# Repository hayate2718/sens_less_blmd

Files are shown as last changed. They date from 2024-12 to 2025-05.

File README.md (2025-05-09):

# センサレスブラシレスモータドライバの基板
FETドライブ基板、MCU基板を基板対基板コネクタでつなげることでモータシステムを構成している。
この構成の利点としては、故障の可能性が高いFETドライブ基板を切り離すことで運用コストの低下、高さ方向に基板をつなげることで下方占有面積の削減を目的としている。
特に、ヒートシンクや電源コネクタ等を基板に搭載すると高さ方向にデッドスペースが多く発生するためその有効利用となる。

## FETドライブ基板サイズ
58.5 x 78.4

## 取付穴ピッチ
52.5 x 49 M3

## 対応ヒートシンク
ヒートシンクの取り付けを前提とした設計をしており優れた放熱効果を実現する。
* ALPHA DCC5923Lシリーズ

## MCU基板インターフェース
* CAN通信用コネクタは2種類基板上に搭載しており、用途に応じて柔軟に対応可能としている。特にRJ45コネクタではCAN以外に12V電源ラインを有しておりLANケーブルのみでの通信電源確保を可能としている。<br>
* 過去にMDを設計した際、組み込みで使うIFのみしか用意しなかった結果ファームウェアの開発が非常にめんどくさくなったため、ロボット組み込み時は使わないがデバッグ用のUARTを装備している。<br>
* UART用の5ピンコネクタには、USB-UART変換によくついている5V電源を入力するピンがあり、5V出力を有するUSB-UART変換であればこれ単体でMCUの起動が可能である。<br>
* MCU基板単体でのデバッグ作業が可能なように電源入力用のコネクタを用意している。さらにFETドライブ基板側にも電源出力があり、GNDラインの絶縁を犠牲にすることでMCU側への電源供給が可能<br>
* MCU基板は5V系IC、3.3V系ICの2系が存在し、5V生成にスイッチング電源を利用し、電源入力を高電圧としバスの電流負荷を軽減することを狙っている。<br>

### 通信ライン
CAN,UART<br>
### 電源
PowerSupply 12V

### RJ45 ピンアサイン
POEのピンアサインに似せている
|Pin num|Function|
|---|---|
|1||
|2||
|3|CANL|
|4|Power_Supply|
|5|Power_Supply|
|6|CANH|
|7|GND|
|8|GND|

## MCUぺりふぇらるあさいん
|Pin num|Pin name|peripheral|note|
|----|----|----|----|
|1|RA7|GPIO IN|CAN ID1|
|2|RB14|NONE||
|3|RB15|QEICMP1|Unsupported|
|4|MCLR|||
|5|VSS|||
|6|VDD|||
|7|RA12|NONE||
|8|RA11|NONE||
|9|RA0|AN0|ADC W_CURRENT|
|10|RA1|NONE||
|11|RB0|AN2|ADC U_CURRENT|
|12|RB1|NONE||
|13|RB2|PGC1||
|14|RB3|PGD1||
|15|AVDD|||
|16|AVSS|||
|17|RC0|QEA1|Unsupported|
|18|RC1|INDX1|Unsupported|
|19|RC2|HOME1|Unsupported|
|20|RC11|NONE||
|21|VSS|||
|22|VDD|||
|23|RA8|QEB1|Unsupported|
|24|RB4|C1TX|CAN_TX|
|25|RA4|C1RX|CAN_RX|
|26|VDD|||
|27|RC12|OSCI||
|28|RC15|OSCO||
|29|VSS|||
|30|RD8|GPIO IN|MD_FAULT|
|31|RB5|GPIO OUT|STAT_LED|
|32|RB6|U1RX|UART_RX|
|33|RC10|NONE||
|34|RB7|U1TX|UART_TX|
|35|RC13|GPIO OUT|FF1_LED(bord err "only input")|
|36|RB8|GPIO OUT|FF2_LED(bord err "only input")|
|37|RB9|NONE||
|38|RC6|PWM6H|MCPWM AHI|
|39|RC7|PWM6L|MCPWM ALO|
|40|RC8|PWM5H|MCPWM BHI|
|41|RC9|PWM5L|MCPWM BLO|
|42|VSS|||
|43|VDD|||
|44|RB10|PWM3H|MCPWM CHI|
|45|RB11|PWM3L|MCPWM CLO|
|46|RB12|GPIO IN|CAN ID4|
|47|RB13|GPIO IN|CAN ID3|
|48|RA10|GPIO IN|CAN ID2|

* VSS IS GND,VDD IS POWER SUPPLY(3.3V),"NONE" MUST BE "INTERNAL PULLUP" OR "GPIO OUT"

## ファームウェアについて
### マイコンについて
MCUにはPIC32MK0512MCJ048を採用しており、32BitPICのなかモータ制御向けとして販売されているものである。<br>
特徴として、専用の直行エンコーダインターフェース(QEI)、モータ制御用PWM(MCPWM)、CANFDが搭載されている。<br>
今回は利用していないがQEIはカウンタパルスのほかにカウンタパルス間の測定も可能となっており、高速域、低速域の領域でエンコーダを有効に利用できるペリフェラルである。<br>
さらに、前回のカウンタリード値と現在のカウンタリード値の差分を記憶するレジスタもあり速度計算も非常に用意に実装可能である。<br>
**QEI便利だね**<br>
モータ制御用PWMではPWMのカウンタマッチ割り込みがあり、これをADCの変換フラグに利用することが可能である。<br>
つまり、センターアラインPWMを利用すればPWM波形の一番安定した場所でADCのデータをペリフェラルのみで取得可能であるということだ。<br>
**これは本当に便利**<br>
トリガポイントはさらに柔軟に設定可能なので、割り込みハンドラを処理するときにはすでに変換データが容易されている状態を作り出すことすら可能である。<br>

### 制御について
6パルスIPDを実装し、磁器突極性を問わず初期位置推定を可能としている。<br>
IPDによって、初期位置を検出し任意の進角で動作を開始し、オープンループで十分なBEMFを取得できる速度域まで動作させる。（ここまではできた）<br>
そこから、FOCに遷移する。予定だった。ort

## コメント
いろいろ能書き書いたけどファーム未完成<br>
現代制御なんもわからん

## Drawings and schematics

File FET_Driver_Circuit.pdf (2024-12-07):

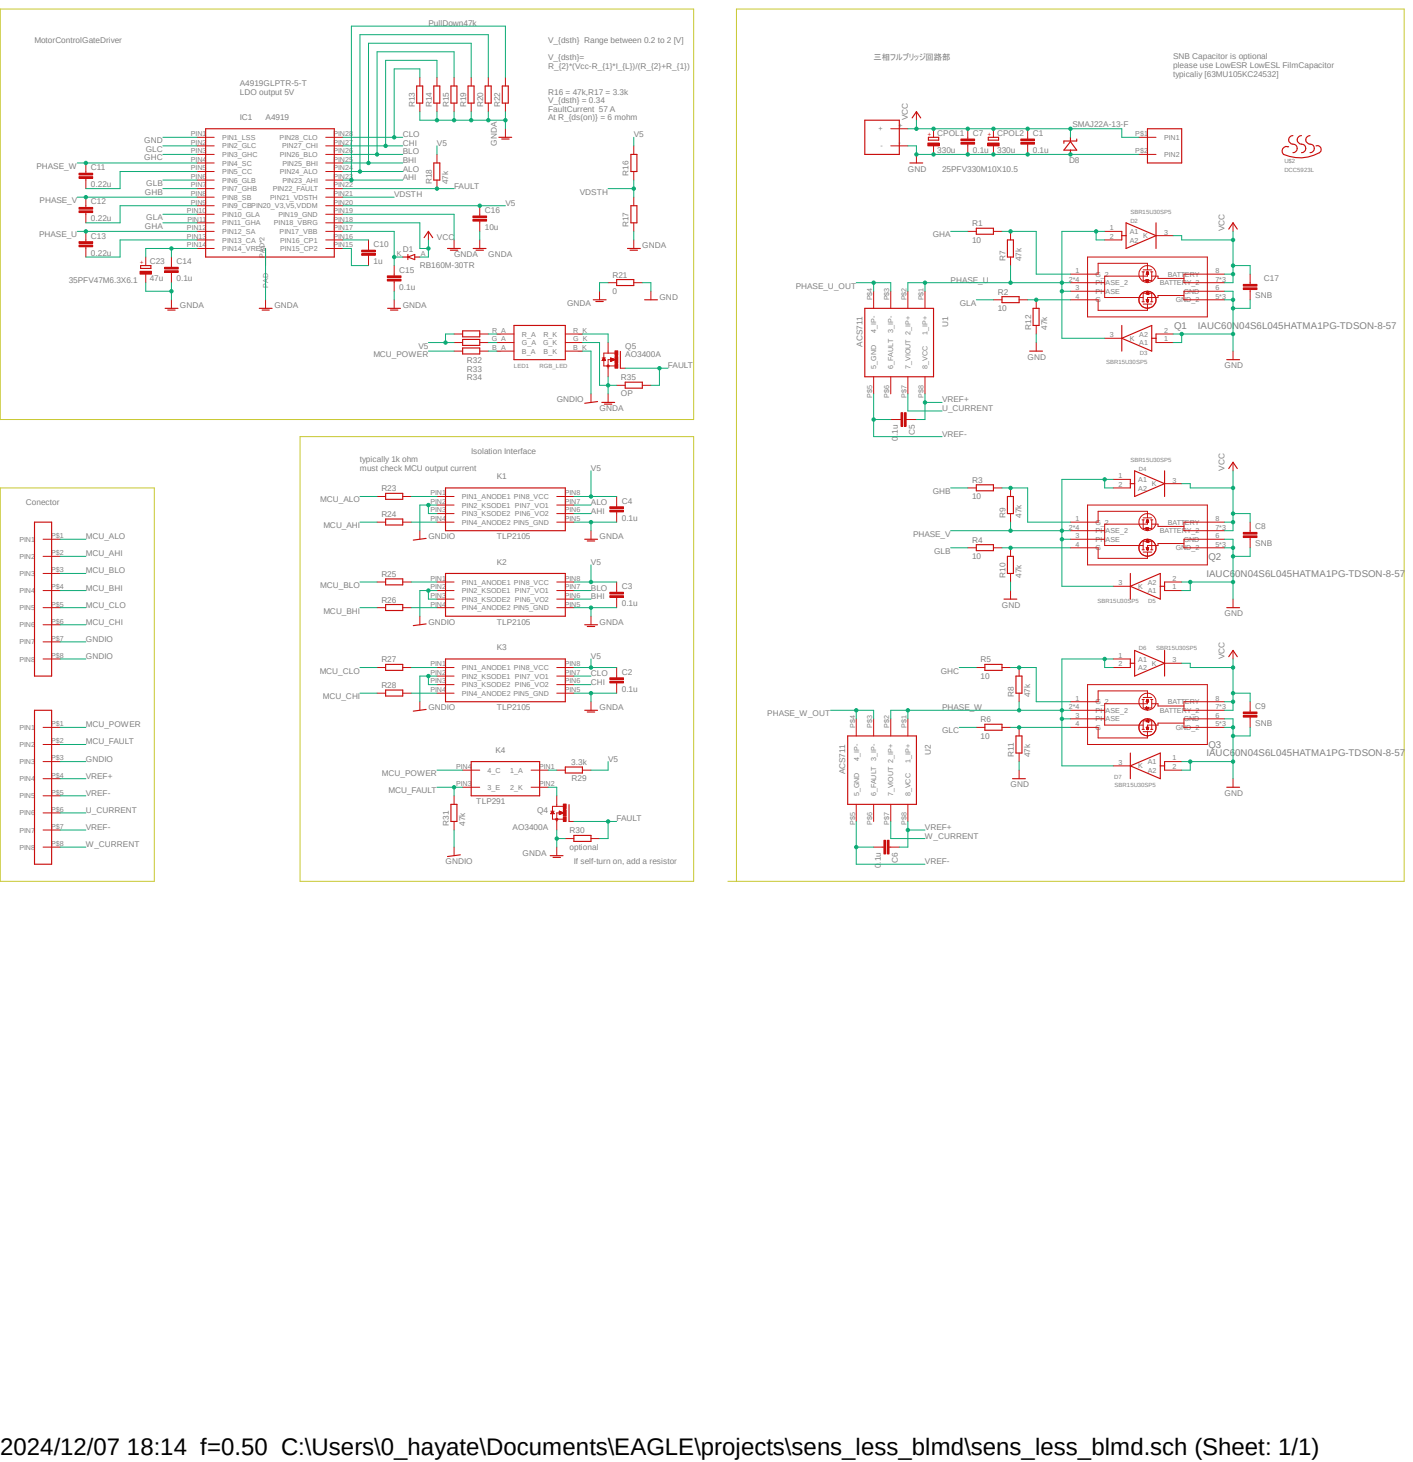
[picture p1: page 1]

SNB Capacitor is optional
please use LowESR LowESL FilmCapacitor
typicaliy [63MU105KC24532]

typically 1k ohm
must check MCU output current

If self-turn on, add a resistor

2024/12/07 18:14 f=0.50 C:\Users\0_hayate\Documents\EAGLE\projects\sens_less_blmd\sens_less_blmd.sch (Sheet: 1/1)

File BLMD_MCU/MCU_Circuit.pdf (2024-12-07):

MCU Debug Interface | UART Interface at 3.3V | MD Interface
Special Power Supply | Special CAN Interface

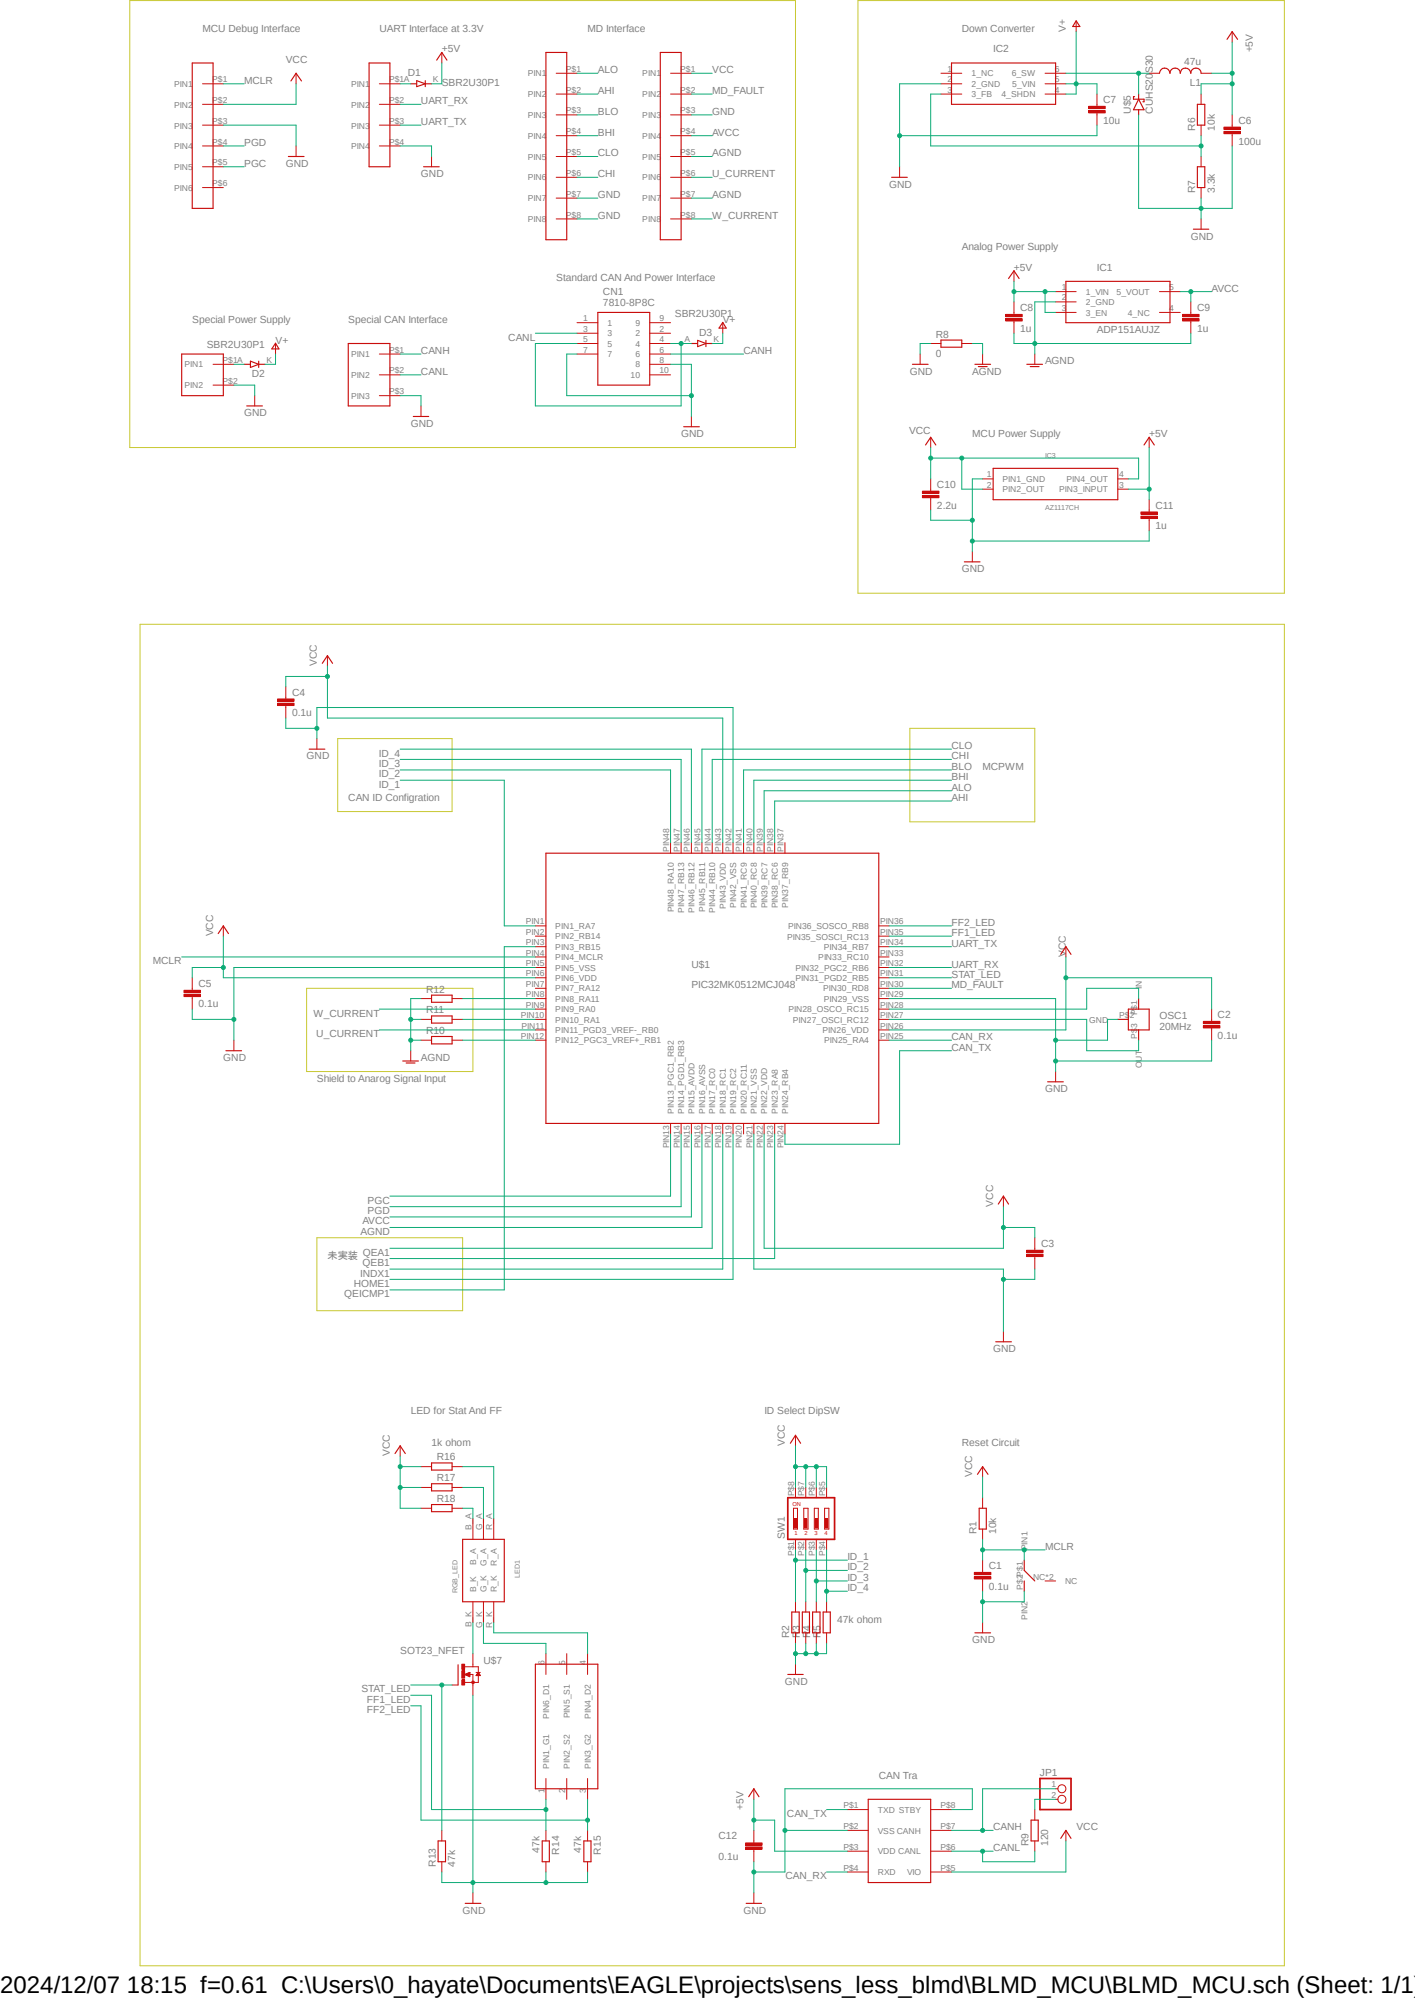
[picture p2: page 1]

Standard CAN And Power Interface

2_GND 2
3_EN 3

Shield to Anarog Signal Input

2024/12/07 18:15 f=0.61 C:\Users\0_hayate\Documents\EAGLE\projects\sens_less_blmd\BLMD_MCU\BLMD_MCU.sch (Sheet: 1/1)

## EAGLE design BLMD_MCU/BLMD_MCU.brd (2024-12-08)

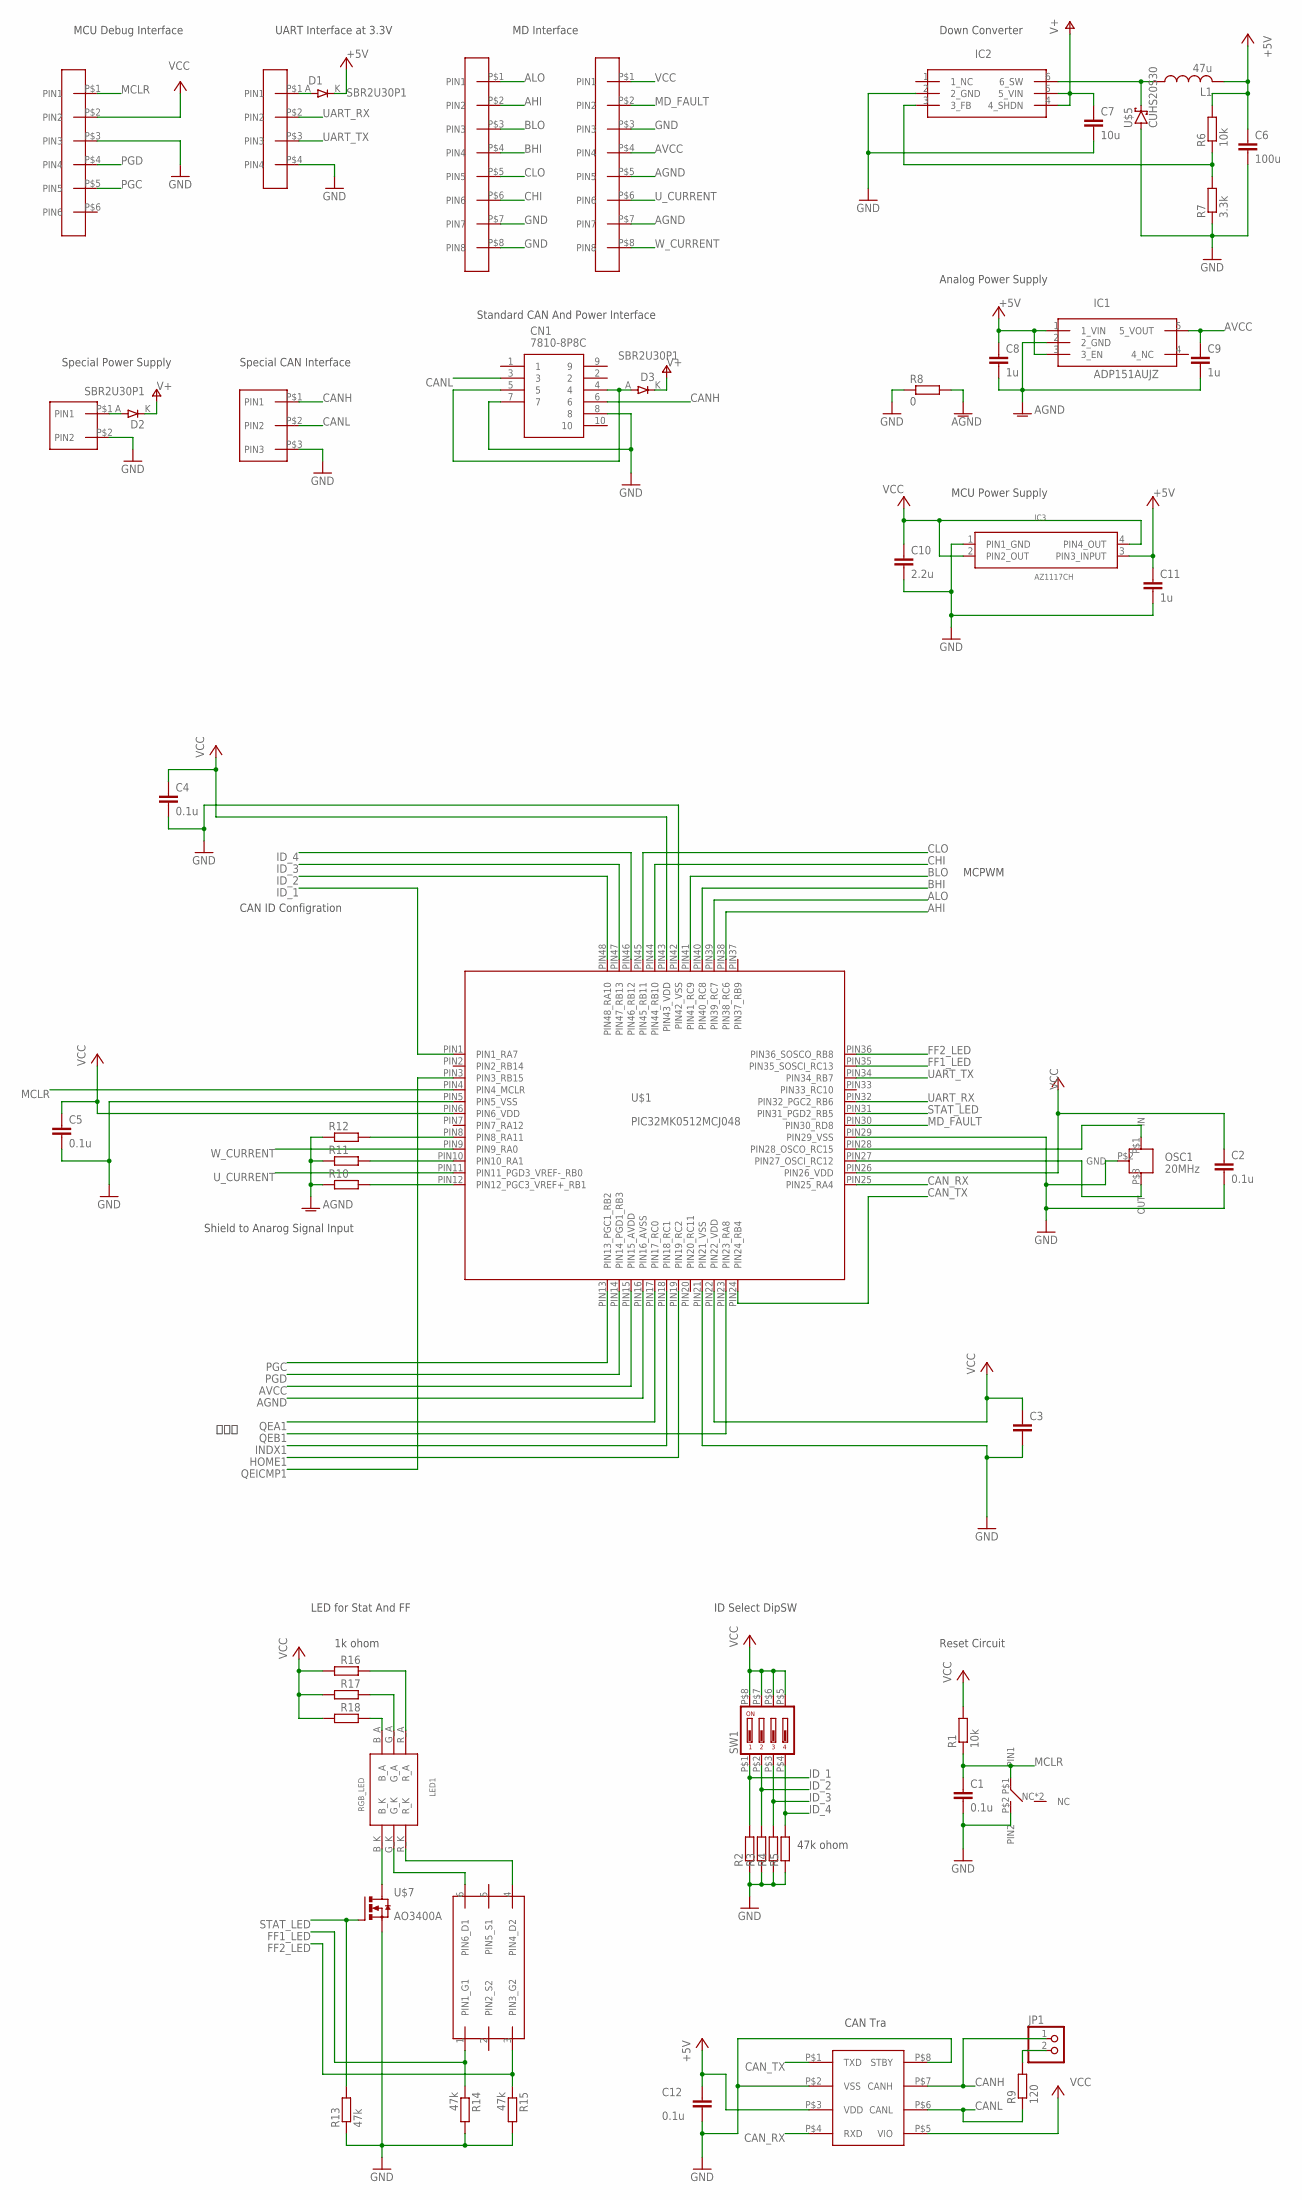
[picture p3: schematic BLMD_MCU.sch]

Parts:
C1, C2, C4, C5, C12: 0.1u; C1608
C3: C-EUC1608; C1608
C6: 100u; C3216
C7: 10u; C1608
C8, C9, C11: 1u; C1608
C10: 2.2u; C1608
CN1: 7810-8P8C; 78108P8C
CON1, CON2: JQ_S8P
CON3: XH_4P
CON4: XH_6P
CON5: XH_3P
D1, D2, D3: SBR2U30P1; SOD_123
IC1: ADP151AUJZ; SOT23-5
IC2: NJW1616T; SOT23-6
IC3: AZ1117CH; SOT223-W
IC4: MCP2562MCP2561-SN; SOIC8
JP1: PINHD-1X2; 1X02
L1: 47u; SMD_INDUCTOR
LED1: RGB_LED
OSC1: 20MHz; CSTNE#
R1, R6: 10k; 1608
R2, R3, R4, R5, R10, R11, R12, R16, R17, R18: R_REG; 1608
R7: 3.3k; 1608
R8: 0; 1608
R9: 120; 1608
R13, R14, R15: 47k; 1608
SW1: DIPSW4
U$1: PIC32MK0512MCJ048; LQFP48PIN
U$2: TAKUTOSUITTI2
U$4: XH_2P
U$5: CUHS20S30; SOD323-W
U$6: FDC6305; SSOT6
U$7: AO3400A; SOT23

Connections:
+5V: C6.1, C8.1, C11.1, C12.1, D1.K (C), IC1.1 (1_VIN), IC1.3 (3_EN), IC3.3 (PIN3_INPUT), IC4.P$3 (VDD), L1.P$2 (2), R6.2
AGND: C8.2, C9.2, CON2.P$5 (PIN5), CON2.P$7 (PIN7), IC1.2 (2_GND), R8.2, R10.1, R11.1, R12.1, U$1.PIN16 (PIN16_AVSS)
AHI: CON1.P$2 (PIN2), U$1.PIN38 (PIN38_RC6)
ALO: CON1.P$1 (PIN1), U$1.PIN39 (PIN39_RC7)
AVCC: C9.1, CON2.P$4 (PIN4), IC1.5 (5_VOUT), U$1.PIN15 (PIN15_AVDD)
BHI: CON1.P$4 (PIN4), U$1.PIN40 (PIN40_RC8)
BLO: CON1.P$3 (PIN3), U$1.PIN41 (PIN41_RC9)
CANH: CN1.6, CON5.P$1 (PIN1), IC4.P$7 (CANH), JP1.1
CANL: CN1.3, CON5.P$2 (PIN2), IC4.P$6 (CANL), R9.1
CAN_RX: IC4.P$4 (RXD), U$1.PIN25 (PIN25_RA4)
CAN_TX: IC4.P$1 (TXD), U$1.PIN24 (PIN24_RB4)
CHI: CON1.P$6 (PIN6), U$1.PIN44 (PIN44_RB10)
CLO: CON1.P$5 (PIN5), U$1.PIN45 (PIN45_RB11)
FF1_LED: R14.1, U$1.PIN35 (PIN35_SOSCI_RC13), U$6.1 (PIN1_G1)
FF2_LED: R15.1, U$1.PIN36 (PIN36_SOSCO_RB8), U$6.3 (PIN3_G2)
GND: C1.2, C2.2, C3.2, C4.2, C5.2, C6.2, C7.2, C10.2, C11.2, C12.2, CN1.7, CN1.8, CON1.P$7 (PIN7), CON1.P$8 (PIN8), CON2.P$3 (PIN3), CON3.P$4 (PIN4), CON4.P$3 (PIN3), CON5.P$3 (PIN3), IC2.2 (2_GND), IC3.1 (PIN1_GND), IC4.P$2 (VSS), IC4.P$8 (STBY), OSC1.P$2 (GND), R2.1, R3.1, R4.1, R5.1, R7.1, R8.1, R13.1, R14.2, R15.2, U$1.PIN5 (PIN5_VSS), U$1.PIN21 (PIN21_VSS), U$1.PIN29 (PIN29_VSS), U$1.PIN42 (PIN42_VSS), U$2.P$2 (PIN2), U$4.P$2 (PIN2), U$5.A, U$7.PIN2 (PIN3_S)
HOME1: U$1.PIN19 (PIN19_RC2)
ID_1: R2.2, SW1.P$1 (1), U$1.PIN1 (PIN1_RA7)
ID_2: R3.2, SW1.P$2 (2), U$1.PIN48 (PIN48_RA10)
ID_3: R4.2, SW1.P$3 (3), U$1.PIN47 (PIN47_RB13)
ID_4: R5.2, SW1.P$4 (4), U$1.PIN46 (PIN46_RB12)
INDX1: U$1.PIN18 (PIN18_RC1)
MCLR: C1.1, CON4.P$1 (PIN1), R1.1, U$1.PIN4 (PIN4_MCLR), U$2.P$1 (PIN1)
MD_FAULT: CON2.P$2 (PIN2), U$1.PIN30 (PIN30_RD8)
unnamed: R12.2, U$1.PIN8 (PIN8_RA11)
unnamed: R11.2, U$1.PIN10 (PIN10_RA1)
unnamed: LED1.B_A, R18.2
unnamed: R10.2, U$1.PIN12 (PIN12_PGC3_VREF+_RB1)
unnamed: OSC1.P$3 (OUT), U$1.PIN27 (PIN27_OSCI_RC12)
unnamed: OSC1.P$1 (IN), U$1.PIN28 (PIN28_OSCO_RC15)
unnamed: LED1.G_A, R17.2
unnamed: JP1.2, R9.2
unnamed: IC2.6 (6_SW), L1.P$1 (1), U$5.C
unnamed: IC2.3 (3_FB), R6.1, R7.2
unnamed: LED1.R_A, R16.2
unnamed: LED1.B_K, U$7.PIN3 (PIN2_D)
unnamed: CON3.P$1 (PIN1), D1.A
unnamed: LED1.G_K, U$6.6 (PIN6_D1)
unnamed: LED1.R_K, U$6.4 (PIN4_D2)
unnamed: D2.A, U$4.P$1 (PIN1)
unnamed: CN1.4, CN1.5, D3.A
PGC: CON4.P$5 (PIN5), U$1.PIN13 (PIN13_PGC1_RB2)
PGD: CON4.P$4 (PIN4), U$1.PIN14 (PIN14_PGD1_RB3)
QEA1: U$1.PIN17 (PIN17_RC0)
QEB1: U$1.PIN23 (PIN23_RA8)
QEICMP1: U$1.PIN3 (PIN3_RB15)
STAT_LED: R13.2, U$1.PIN31 (PIN31_PGD2_RB5), U$7.PIN1 (PIN1_G)
UART_RX: CON3.P$2 (PIN2), U$1.PIN32 (PIN32_PGC2_RB6)
UART_TX: CON3.P$3 (PIN3), U$1.PIN34 (PIN34_RB7)
U_CURRENT: CON2.P$6 (PIN6), U$1.PIN11 (PIN11_PGD3_VREF-_RB0)
V+: C7.1, D2.K (C), D3.K (C), IC2.4 (4_SHDN), IC2.5 (5_VIN)
VCC: C2.1, C3.1, C4.1, C5.1, C10.1, CON2.P$1 (PIN1), CON4.P$2 (PIN2), IC3.2 (PIN2_OUT), IC3.4 (PIN4_OUT), IC4.P$5 (VIO), R1.2, R16.1, R17.1, R18.1, SW1.P$5 (5), SW1.P$6 (6), SW1.P$7 (7), SW1.P$8 (8), U$1.PIN6 (PIN6_VDD), U$1.PIN22 (PIN22_VDD), U$1.PIN26 (PIN26_VDD), U$1.PIN43 (PIN43_VDD)
W_CURRENT: CON2.P$8 (PIN8), U$1.PIN9 (PIN9_RA0)

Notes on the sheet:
Shield to Anarog Signal Input
未実装
47k ohom
1k ohom
MCPWM
CAN ID Configration
MD Interface
UART Interface at 3.3V
MCU Debug Interface
Special Power Supply
Special CAN Interface
Standard CAN And Power Interface
Analog Power Supply
MCU Power Supply
Down Converter
LED for Stat And FF
ID Select DipSW
Reset Circuit
CAN Tra

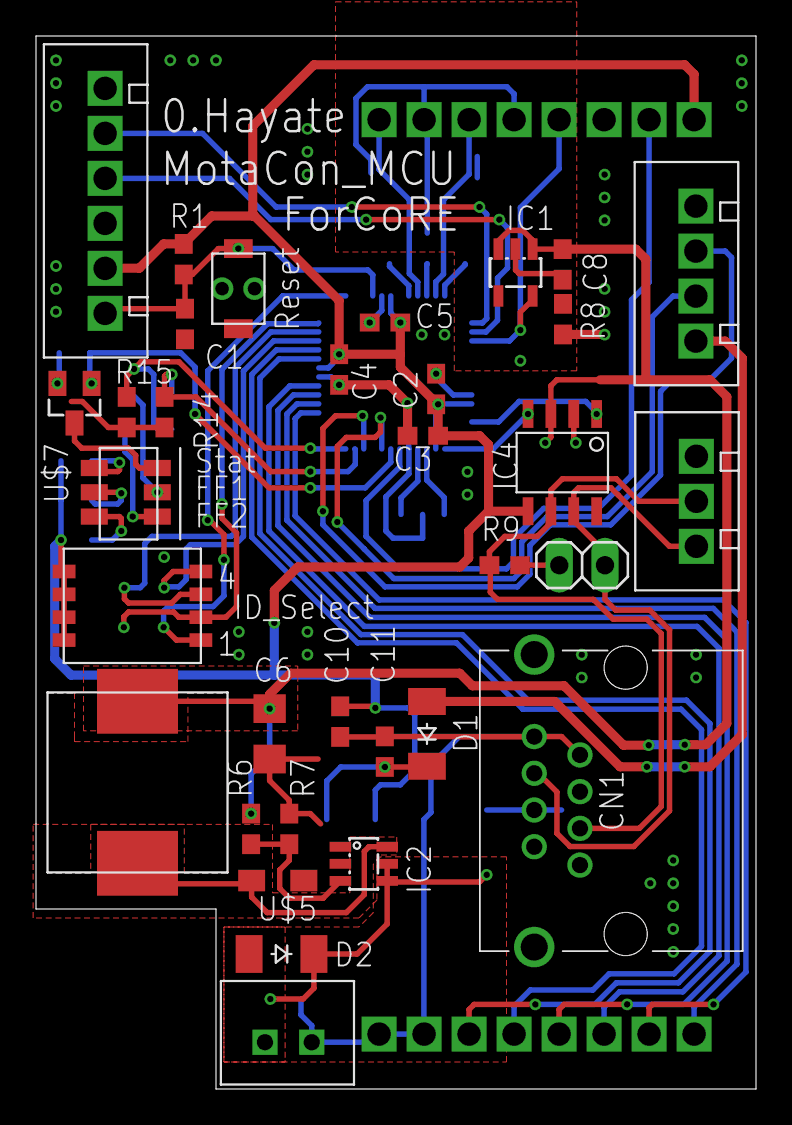
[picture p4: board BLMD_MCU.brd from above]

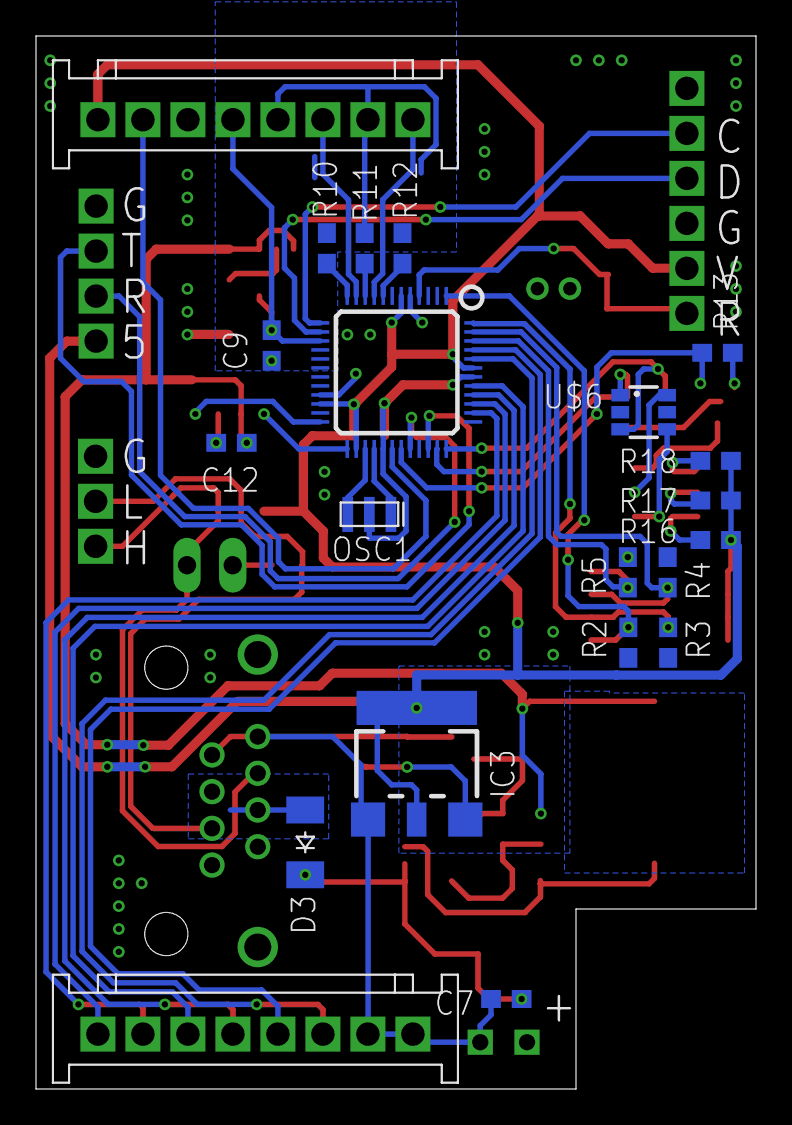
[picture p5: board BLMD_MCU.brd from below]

Board: 2 copper layers, 40.0 x 58.5 mm, 54 parts (21 on the bottom side), 48 nets.

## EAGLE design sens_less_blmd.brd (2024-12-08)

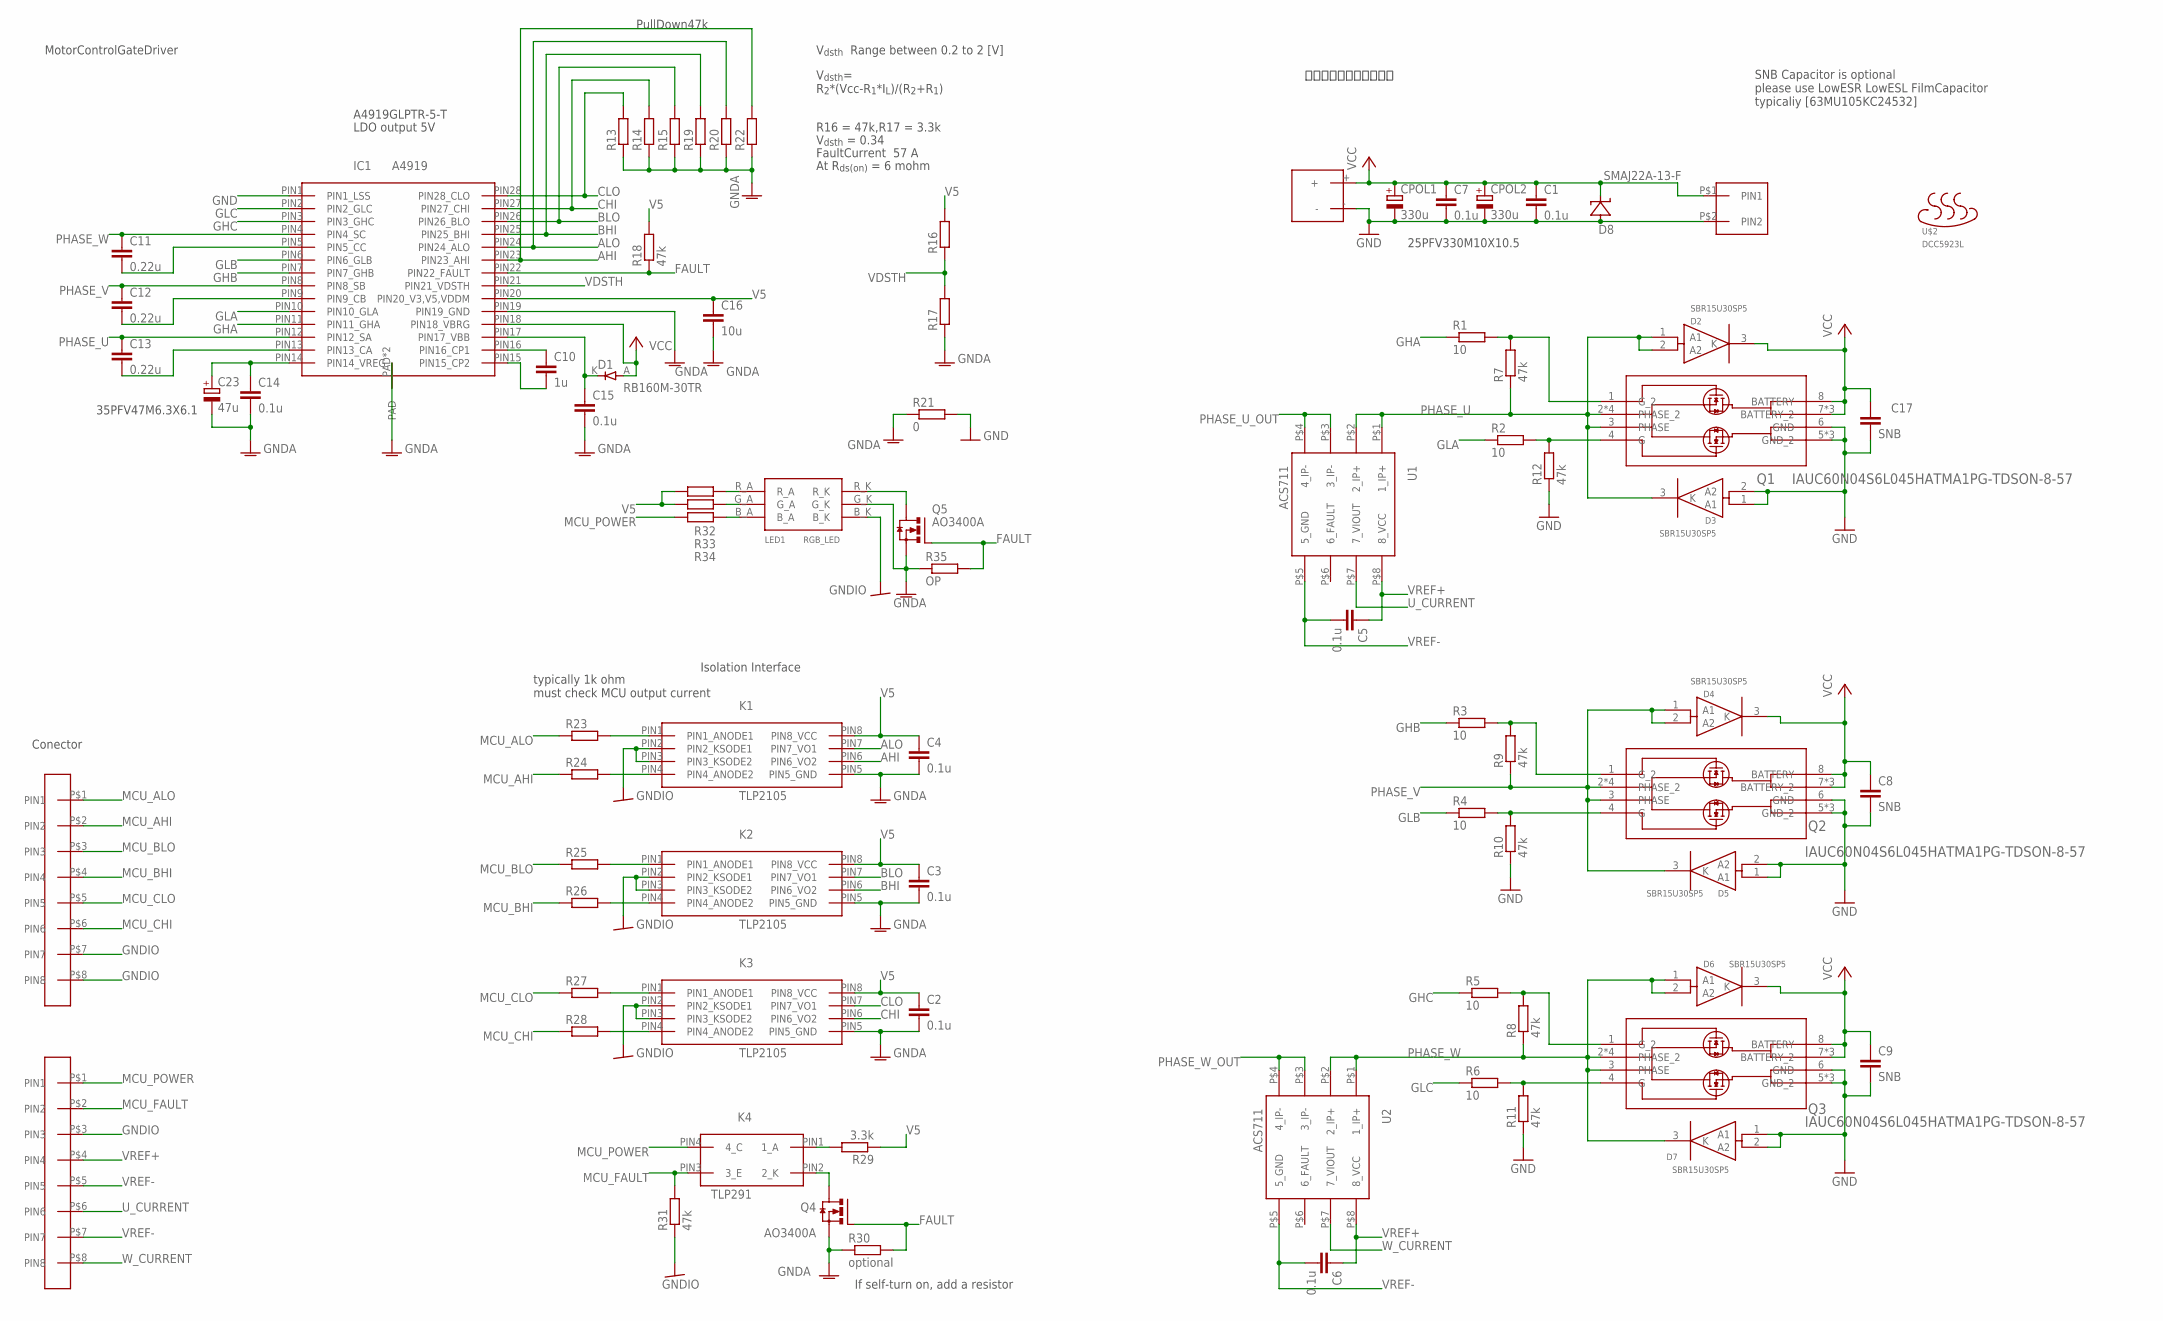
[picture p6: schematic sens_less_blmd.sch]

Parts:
C1, C2, C3, C4, C5, C6, C7, C14, C15: 0.1u; C1608
C8, C9, C17: SNB; C4532
C10: 1u; C1608
C11, C12, C13: 0.22u; C1608
C16: 10u; C1608
C23: 47u; 153CLV-0605
CON1, CON2: XH_8P
CPOL1, CPOL2: 330u; 1014CAPA
D1: RB160M-30TR; SOD_123
D2, D3, D4, D5, D6, D7: SBR15U30SP5; POWERDI_5
D8: SMAJ22A-13-F; DO-214AC
IC1: A4919; TSSOP_28P_ALLEGRO_E
K1, K2, K3: TLP2105; SOP8
K4: TLP291
LED1: RGB_LED
Q1, Q2, Q3: IAUC60N04S6L045HATMA1PG-TDSON-8-57; PG-TDSON-8-57
Q4, Q5: AO3400A; SOT23
R1, R2, R3, R4, R5, R6: 10; 1608
R7, R8, R9, R10, R11, R12, R18, R31: 47k; 1608
R13, R14, R15, R16, R17, R19, R20, R22, R23, R24, R25, R26, R27, R28, R32, R33, R34: R_REG; 1608
R21: 0; 1608
R29: 3.3k; 1608
R30: optional; 1608
R35: OP; 1608
U1, U2: ACS711; SOIC8
U$1: XH_2P
U$2: DCC5923L
U$22: XT60

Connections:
AHI: IC1.PIN23 (PIN23_AHI), K1.PIN6 (PIN6_VO2), R22.2
ALO: IC1.PIN24 (PIN24_ALO), K1.PIN7 (PIN7_VO1), R20.2
BHI: IC1.PIN25 (PIN25_BHI), K2.PIN6 (PIN6_VO2), R19.2
BLO: IC1.PIN26 (PIN26_BLO), K2.PIN7 (PIN7_VO1), R15.2
CHI: IC1.PIN27 (PIN27_CHI), K3.PIN6 (PIN6_VO2), R14.2
CLO: IC1.PIN28 (PIN28_CLO), K3.PIN7 (PIN7_VO1), R13.2
FAULT: IC1.PIN22 (PIN22_FAULT), Q4.PIN1 (PIN1_G), Q5.PIN1 (PIN1_G), R18.1, R30.2, R35.2
GHA: IC1.PIN11 (PIN11_GHA), R1.1
GHB: IC1.PIN7 (PIN7_GHB), R3.1
GHC: IC1.PIN3 (PIN3_GHC), R5.1
GLA: IC1.PIN10 (PIN10_GLA), R2.1
GLB: IC1.PIN6 (PIN6_GLB), R4.1
GLC: IC1.PIN2 (PIN2_GLC), R6.1
GND: C1.2, C7.2, C8.2, C9.2, C17.2, CPOL1.-, CPOL2.-, D3.1 (A1), D3.2 (A2), D5.1 (A1), D5.2 (A2), D7.1 (A1), D7.2 (A2), D8.A, IC1.PIN1 (PIN1_LSS), Q1.5 (GND_2), Q1.6 (GND), Q1.SPAD (GND_2), Q1.SPAD@1 (GND_2), Q2.5 (GND_2), Q2.6 (GND), Q2.SPAD (GND_2), Q2.SPAD@1 (GND_2), Q3.5 (GND_2), Q3.6 (GND), Q3.SPAD (GND_2), Q3.SPAD@1 (GND_2), R10.1, R11.1, R12.1, R21.2, U$1.P$2 (PIN2), U$22.-
GNDA: C2.2, C3.2, C4.2, C14.2, C15.2, C16.2, C23.-, IC1.PAD, IC1.PAD@14 (PAD), IC1.PIN19 (PIN19_GND), K1.PIN5 (PIN5_GND), K2.PIN5 (PIN5_GND), K3.PIN5 (PIN5_GND), LED1.G_K, Q4.PIN2 (PIN3_S), Q5.PIN2 (PIN3_S), R13.1, R14.1, R15.1, R17.1, R19.1, R20.1, R21.1, R22.1, R30.1, R35.1
GNDIO: CON1.P$3 (PIN3), CON2.P$7 (PIN7), CON2.P$8 (PIN8), K1.PIN2 (PIN2_KSODE1), K1.PIN3 (PIN3_KSODE2), K2.PIN2 (PIN2_KSODE1), K2.PIN3 (PIN3_KSODE2), K3.PIN2 (PIN2_KSODE1), K3.PIN3 (PIN3_KSODE2), LED1.B_K, R31.1
MCU_AHI: CON2.P$2 (PIN2), R24.1
MCU_ALO: CON2.P$1 (PIN1), R23.1
MCU_BHI: CON2.P$4 (PIN4), R26.1
MCU_BLO: CON2.P$3 (PIN3), R25.1
MCU_CHI: CON2.P$6 (PIN6), R28.1
MCU_CLO: CON2.P$5 (PIN5), R27.1
MCU_FAULT: CON1.P$2 (PIN2), K4.PIN3 (3_E), R31.2
MCU_POWER: CON1.P$1 (PIN1), K4.PIN4 (4_C), R34.1
unnamed: Q1.1 (G_2), R1.2, R7.2
unnamed: Q1.4 (G), R2.2, R12.2
unnamed: Q2.4 (G), R4.2, R10.2
unnamed: LED1.B_A, R34.2
unnamed: Q3.1 (G_2), R5.2, R8.2
unnamed: Q3.4 (G), R6.2, R11.2
unnamed: C10.1, IC1.PIN16 (PIN16_CP1)
unnamed: C10.2, IC1.PIN15 (PIN15_CP2)
unnamed: C14.1, C23.+, IC1.PIN14 (PIN14_VREG)
unnamed: K1.PIN1 (PIN1_ANODE1), R23.2
unnamed: K1.PIN4 (PIN4_ANODE2), R24.2
unnamed: K2.PIN1 (PIN1_ANODE1), R25.2
unnamed: K2.PIN4 (PIN4_ANODE2), R26.2
unnamed: K3.PIN1 (PIN1_ANODE1), R27.2
unnamed: C13.2, IC1.PIN13 (PIN13_CA)
unnamed: C12.2, IC1.PIN9 (PIN9_CB)
unnamed: C11.2, IC1.PIN5 (PIN5_CC)
unnamed: K3.PIN4 (PIN4_ANODE2), R28.2
unnamed: K4.PIN2 (2_K), Q4.PIN3 (PIN2_D)
unnamed: C15.1, D1.K (C), IC1.PIN17 (PIN17_VBB)
unnamed: K4.PIN1 (1_A), R29.2
unnamed: Q2.1 (G_2), R3.2, R9.2
unnamed: LED1.G_A, R33.2
unnamed: LED1.R_A, R32.2
unnamed: LED1.R_K, Q5.PIN3 (PIN2_D)
PHASE_U: C13.1, D2.1 (A1), D2.2 (A2), D3.3 (K), IC1.PIN12 (PIN12_SA), Q1.2 (PHASE_2), Q1.3 (PHASE), Q1.SDPAD (PHASE_2), Q1.SDPAD@1 (PHASE_2), Q1.SDPAD@2 (PHASE_2), R7.1, U1.P$1 (1_IP+), U1.P$2 (2_IP+)
PHASE_U_OUT: U1.P$3 (3_IP-), U1.P$4 (4_IP-)
PHASE_V: C12.1, D4.1 (A1), D4.2 (A2), D5.3 (K), IC1.PIN8 (PIN8_SB), Q2.2 (PHASE_2), Q2.3 (PHASE), Q2.SDPAD (PHASE_2), Q2.SDPAD@1 (PHASE_2), Q2.SDPAD@2 (PHASE_2), R9.1
PHASE_W: C11.1, D6.1 (A1), D6.2 (A2), D7.3 (K), IC1.PIN4 (PIN4_SC), Q3.2 (PHASE_2), Q3.3 (PHASE), Q3.SDPAD (PHASE_2), Q3.SDPAD@1 (PHASE_2), Q3.SDPAD@2 (PHASE_2), R8.1, U2.P$1 (1_IP+), U2.P$2 (2_IP+)
PHASE_W_OUT: U2.P$3 (3_IP-), U2.P$4 (4_IP-)
U_CURRENT: CON1.P$6 (PIN6), U1.P$7 (7_VIOUT)
V5: C2.1, C3.1, C4.1, C16.1, IC1.PIN20 (PIN20_V3,V5,VDDM), K1.PIN8 (PIN8_VCC), K2.PIN8 (PIN8_VCC), K3.PIN8 (PIN8_VCC), R16.2, R18.2, R29.1, R32.1, R33.1
VCC: C1.1, C7.1, C8.1, C9.1, C17.1, CPOL1.+, CPOL2.+, D1.A, D2.3 (K), D4.3 (K), D6.3 (K), D8.C, IC1.PIN18 (PIN18_VBRG), Q1.7 (BATTERY_2), Q1.8 (BATTERY), Q1.DPAD (BATTERY_2), Q1.DPAD@1 (BATTERY_2), Q2.7 (BATTERY_2), Q2.8 (BATTERY), Q2.DPAD (BATTERY_2), Q2.DPAD@1 (BATTERY_2), Q3.7 (BATTERY_2), Q3.8 (BATTERY), Q3.DPAD (BATTERY_2), Q3.DPAD@1 (BATTERY_2), U$1.P$1 (PIN1), U$22.+
VDSTH: IC1.PIN21 (PIN21_VDSTH), R16.1, R17.2
VREF+: C5.1, C6.1, CON1.P$4 (PIN4), U1.P$8 (8_VCC), U2.P$8 (8_VCC)
VREF-: C5.2, C6.2, CON1.P$5 (PIN5), CON1.P$7 (PIN7), U1.P$5 (5_GND), U2.P$5 (5_GND)
W_CURRENT: CON1.P$8 (PIN8), U2.P$7 (7_VIOUT)

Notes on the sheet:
三相フルブリッジ回路部
A4919GLPTR-5-T
LDO output 5V
PullDown47k
typically 1k ohm must check MCU output current
If self-turn on, add a resistor
Isolation Interface
MotorControlGateDriver
V_{dsth} Range between 0.2 to 2 [V]
At R_{ds(on)} = 6 mohm
V_{dsth}= R_{2}*(Vcc-R_{1}*I_{L})/(R_{2}+R_{1})
V_{dsth} = 0.34
FaultCurrent 57 A
R16 = 47k,R17 = 3.3k
Conector
SNB Capacitor is optional please use LowESR LowESL FilmCapacitor typicaliy [63MU105KC24532]
25PFV330M10X10.5
35PFV47M6.3X6.1

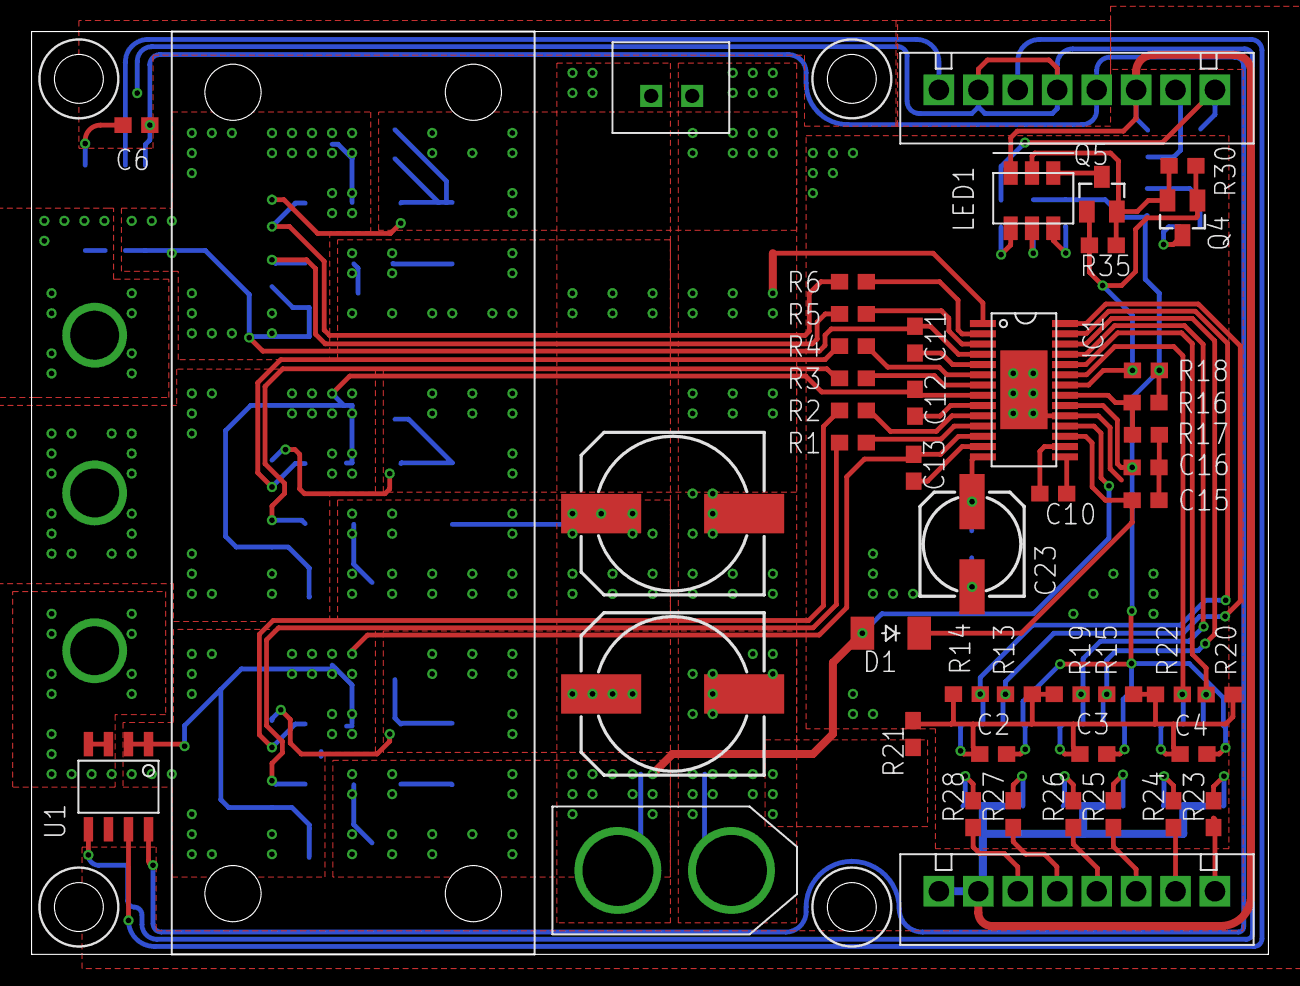
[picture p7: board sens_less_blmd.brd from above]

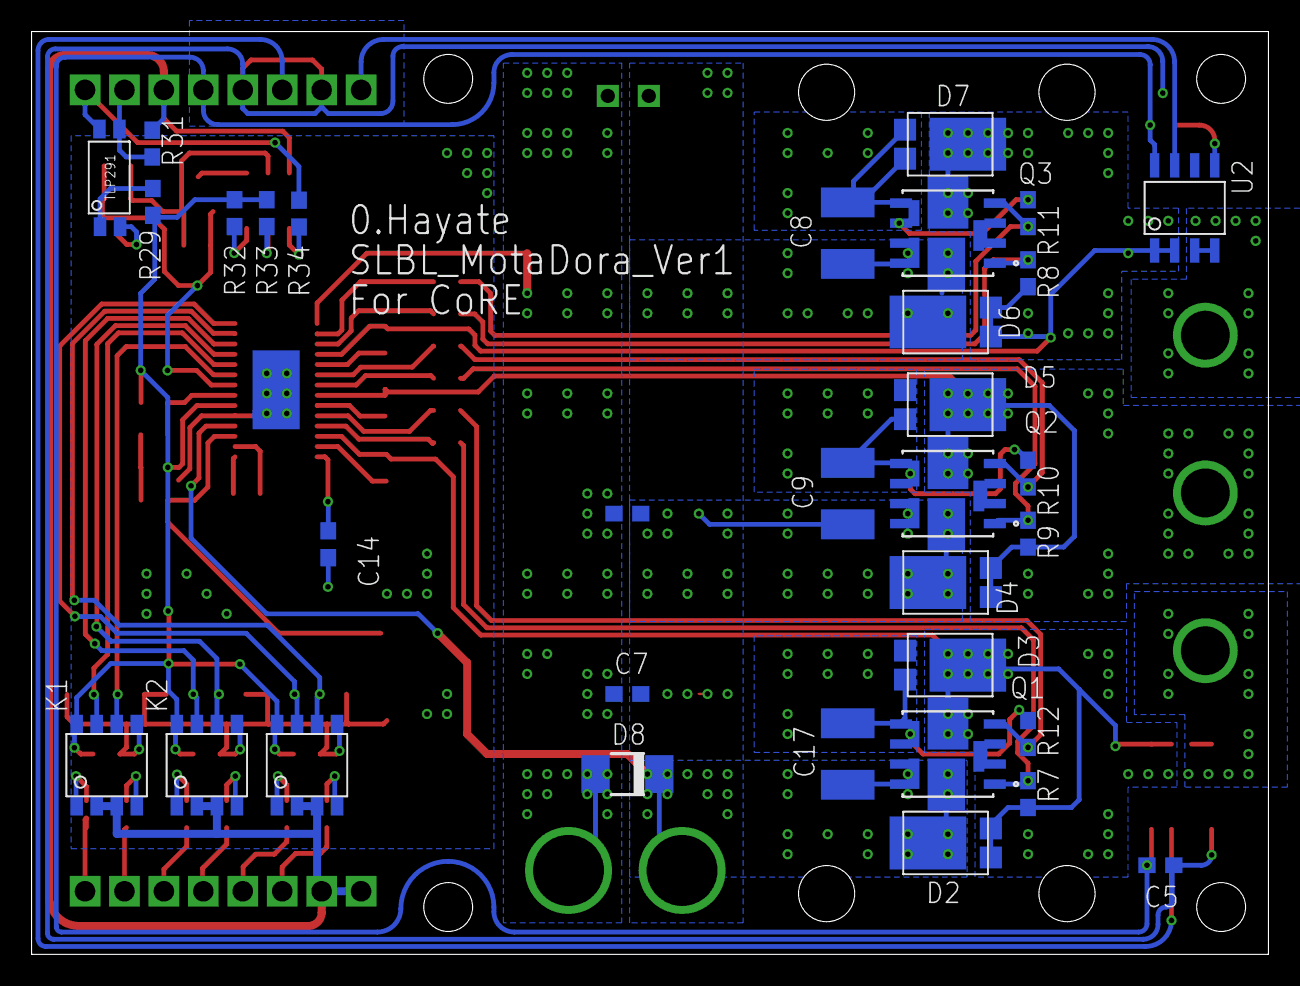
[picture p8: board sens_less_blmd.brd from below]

Board: 2 copper layers, 78.4 x 58.5 mm, 81 parts (33 on the bottom side), 61 nets.

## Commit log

2020-11-07 ファイル追加
    [sens_less_blmd.brd, sens_less_blmd.sch]
2020-11-21 インバータ部を設計した
    [sens_less_blmd.brd, sens_less_blmd.sch]
2020-11-21 ドライバ側回路図の完成
    [sens_less_blmd.brd, sens_less_blmd.sch]
2021-01-09 電流センサの測定位置を変えた
    [sens_less_blmd.brd, sens_less_blmd.sch]
2022-01-20 配置を大まかにきめた
    [sens_less_blmd.brd, sens_less_blmd.sch]
2022-02-01 配置を少し整えた
    [sens_less_blmd.brd, sens_less_blmd.sch]
2024-11-24 回路図を作成
    [sens_less_blmd.brd, sens_less_blmd.sch]
2024-11-30 fet側基板の完成とガーバーファイル追加
    [BLMD_MCU.brd, BLMD_MCU.sch, sens_less_blmd.brd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]
2024-12-01 UVW結線のふっとぷりんと追加、新ガーバーファイル追加
    [BLMD_MCU.brd, BLMD_MCU.sch, sens_less_blmd.brd]
2024-12-05 MCU側回路図を作成
    [BLMD_MCU.brd, BLMD_MCU.sch]
2024-12-07 基板完成 ガーバーファイル追加
    [BLMD_MCU.brd, BLMD_MCU.sch]
2024-12-07 ファイルの追加
2024-12-08 ガーバーファイル追加
    [BLMD_MCU.brd, BLMD_MCU.sch, sens_less_blmd.brd]

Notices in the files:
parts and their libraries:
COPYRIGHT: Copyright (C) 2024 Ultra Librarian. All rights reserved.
